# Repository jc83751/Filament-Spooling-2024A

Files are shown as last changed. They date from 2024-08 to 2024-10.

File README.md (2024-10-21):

# Filament-Spooling-2024A
DMMS Autumn 2024 - Filament Spooling Project.
Hello,
the material you see here was created in a 12 week period for a university subject. We hope that the compilation of materials produced
will be of good use to you.

You are free to use this in any way you like, however, should you publish anything from here please credit 
us for any work or research we have conducted as this took a lot of time and effort.

REF: Chu, J., Luu, M., Harris, J. & Do, D. (2024, August). _Filament Spooling 2024A_. GitHub repository. https://github.com/jc83751/Filament-Spooling-2024A

-J.C.

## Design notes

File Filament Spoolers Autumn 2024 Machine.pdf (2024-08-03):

# P20 – Filament Spoolers Design Documentation for DMMS Autumn 2024

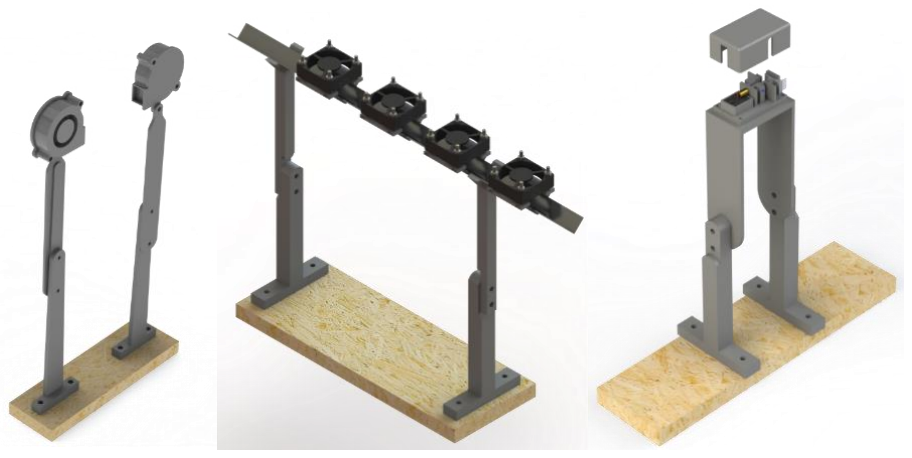
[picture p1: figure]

Project/ID
Plastic Filament Extruder for 3D Printing (P20) Clients

Richard Jamie
Marc Carmichael
Team

Jeremy Chu (14178077)

Johnathan Harris (13246160)

Duc Do (14317655)
Mark Luu (13199118)
Affiliation

UTS / ProtoSpace

43019 DMMS – P20 – Autumn 2024 – Filament Spoolers

2 | P a g e

## Table of Contents

## 1. Project Summary

### 1.1. Problem Statement

UTS staff, in specific, UTS ProtoSpace and FEIT, require the design of a filament spooler compatible with existing extruding technology that can produce 3D printing filament with consistent diameter (1.75 mm ±0.3 mm) and quality using recycled 3D prints and experimental materials. A system will be designed, allowing for the implementation of the filament spooler into existing operation, clarifying the feasibility and capabilities of the recycled or experimental 3D printing extruded filament in physicality.

### 1.2. Project Objectives

Key objectives are presented here as determined based on the functional requirements list and the evaluation criteria.

- Consistent Quality Filament Produced – The filament produced is of a diameter 1.75 mm with a tolerance of ±0.3 mm; the filament produced has consistent material properties throughout and deformation is minimised.
- Customisable Settings – The filament spooler has adjustable settings to accommodate a wide range of materials.
- Modular Design – The filament spooler is easy to assemble, upgrade, and has scalability for more general applications.
- Ease of Maintenance and Resources – The system of the filament spooler is easy to inspect, allowing for simple troubleshooting and official parts can be sourced domestically for change/replacement.
- Acceptable Efficiency – The filament spooler can produce a suitable amount of filament with minimal wastage.

### 1.3. Project Deliverables

Key Goals

- Filament Spooler – A functional model of the filament spooler capable of producing consistent-quality 3D printing filament using recycled 3D prints and experimental materials.
- Design and Next Steps Documentation – Basic instructions of operation, detailed technical drawings, schematics, and specifications of the filament spooler design, including assembly instructions and Bill of Materials (BOM).
- Filament Quality Assessment – Documentation of filament quality assessment procedures and results, mainly the measurements of diameter but may include material other properties.

Stretch Goals

- Machine Performance Evaluation – A report that evaluates the performance of the filament spooler involving efficiency, general reliability, and sustainability (e.g., plastic saved from landfill and electricity usage).
- Integration Plan – A proposed plan for the integration of the filament spooler at UTS, this could potentially involve collaboration with faculties such as Design, Architecture, and Building (DAB), FEIT Students, UTS Startups.
- Operation Manual – A user-friendly manual providing instructions for operating, maintaining, and troubleshooting the filament spooler.

## 2. Project Budget and Tasks

### 2.1. Project Budget and Plan

For this project, the P20 Team worked with a $600 AUD budget with flexibility regarding increases should it be required. This was presented in a client contract document where some key milestones were also proposed (see Table 1.) and agreed upon prior to starting work. It should be noted however that these were general milestones with the final delivery of the product occurring much later and in segments (agreed upon by the clients).

Table 1. Original Key Milestones Agreed Upon on 28/03/24
Task – Description | Expected Working Time | Approx. Start Time | Approx. Finishing Date
Project Scoping – Stakeholders interviewed to develop requirements and scope. Research conducted to guide activities and defined scope boundaries. Functional requirements and evaluation criteria will be created to validate the deliverables. | ~4 weeks | Start Week 2 | End Week 4
Translate and ideate – Stakeholder statements and needs are further refined to develop design concepts. Multiple designs will be presented and reviewed for the suitability of the project. | ~3 weeks | Start Week 4 | End Week 4
Refined Ideation – Design concepts, specifications, and ideas converge to a solution based on stakeholder(s) feedback and assessment. Rudimentary CAD and sketches will be developed to form a baseline for the chosen solution. | ~1 week | Start Week 4 | End Week 5
Prototype and Testing – Building a rudimentary model and testing its viability will be conducted to enable for refinement according to the evaluation criteria and functional requirements. | ~6 weeks | Start Week 6 | End Week 9
Deliverables (Documentation) – Design documentation, quality assessments, integration plans, performance evaluation, and an operation manual will be made. | ~7 weeks | Start Week 6 | End Week 12
Final Product (Gold Copy) – A product in an acceptable working state for the client is delivered. | ~11 weeks | Start Week 2 | End Week 12

Note that the week start, and ends are according to the UTS timetable as of 2024 – Autumn.

### 2.2. Project Tasks and Activities

There are many tasks and activities which were shared amongst P20 group members, these are nested amongst the design process (see Figure 1.). As such, only specific descriptions of tasks and activities will be briefly discussed.

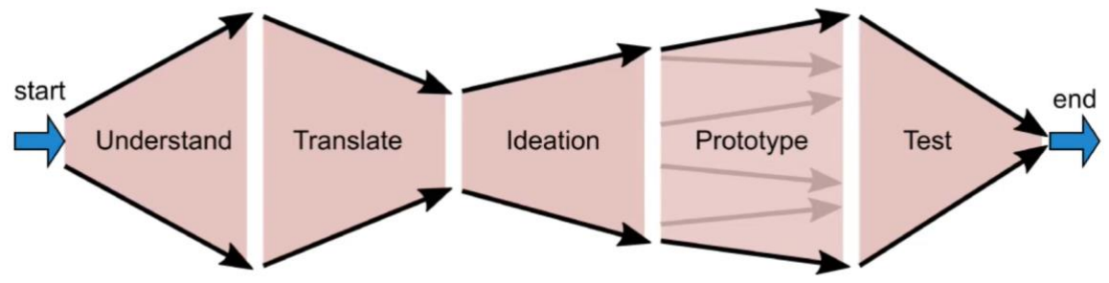
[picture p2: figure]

Figure 1. Overview of the Design Process (Carmichael, 2017). The main project tasks and activities undertaken in this project were:

- Scheduling tasks – Tasks to be scheduled amongst team members to prevent overlap, set-up accountability, and increase efficiency.
- Analysis and measurement of starting parameters
- Measurement of the Desktop SJ35 parameters (general dimensions, extrusion parameters, etc.).
- Analysis of previous groups work (in this case there was none).
- Properties of plastic pellets.
- Review of existing technology (literature review).
- Ordering of materials – Important to be done ASAP as delays are common (in this case there was a 4–5-week delay).
- CAD modelling
- Rapid prototyping of components in computer space.
- Construction of models for assembly.
- Sketching of drawings for documentation.
- Building and testing
- Translation of computer sketches to tangible components in a physical system.
- Testing of performance of the constructed system using experiments.
- Further iteration of constructed system.
- Documentation – Documentation of processes experienced, achievements, how to replicate experiments/results is crucial for the further development of an idea.

## 3. Responsibilities and Expectations

### 3.1. Cooling Subsystem

3.1.1. Responsibilities:
The cooling subsystem is an essential role of the extrusion process that manages the immediate heat dissipation of the filament and thereby, shrinking to a desired diameter. The responsibilities include having uniform rapid cooling, modular design such that the layout is interchangeable to accommodate and maintain compatibility of the other subsystems, and a design architecture that can self-adjust accordingly to variable conditions throughout the duration of the extrusion operation. Implementing controlled cooling minimises the effect of filament deformation and sustains the ideal material properties of the filament suitable for 3D printing.
3.1.2. Expectations:
The subsystem is expected to be simplistic, but modular like a closed feedback loop where real-time information such as the temperature and diameter size of the filament is known and self-calibrates to ensure the filament maintains within the 1.75 +/- 0.3 mm range. Cooling of filament to form a durable surface is crucial for it to be processed further in measuring and tensioning stages.

### 3.2. Measuring Subsystem

3.2.1. Responsibilities:
The measuring subsystem is a control design that allows the extruded filament to maintain the expected diameter. The laser system is controlled by an Arduino. The major function is to determine the drop in lux through the filament and thereby, use this conversion to determine the instantaneous diameter upon contact. The system is expected to be autonomous and does not require further input after starting operation.
3.2.2. Expectations:
The systems are expected to measure and convert the lux to the millimetres which is the diameters of the filament. This data is then used to ensure the filament is at the required 1.75mm diameter. If the filament is too small, the system will send a signal to the tensioning system to slow down so that the filament diameter increases. Similarly, If the filament is too big, the system will send a signal to the tensioning systems to increase the speed of pulling to decrease the diameters of filament.

### 3.3. Tensioning Subsystem

3.3.1. Responsibilities:
The tensioning system is the element which enables the precise control of filament diameter by effect of shear thinning. The assembly consists of Arduino-controlled rollers which grip and “pull” on freshly extruded and cooled filament at specific speeds to achieve diameter consistency. The relationship explained in brief is as follows:
- Faster roller speed = Thinner filament diameter, risk of snapping or stretching the filament too thin.
- Slower roller speed = Larger filament diameter, risk of clogging machine should the filament bunch up.
As such, it is critical that the extrusion rate of the extruder, the tensioning speed is finely tuned with the specific properties of a material to acquire a “goldilocks” zone of filament diameter (1.75 mm ±0.3 mm). Ideally, the speed of this system is informed by the results from the measuring subassembly.
3.3.2. Expectations:
The system is expected to be easily controlled using Arduino code using a specified speed according to the material extruded and the extrusion machine parameters. The system is also expected to not deform by squishing filament through its rollers, like soft pliable material such as TPU should be used to prevent unintentional deformation. Alternatively, an alternative spring type may be used according to material desired to be extruded and spooled.

### 3.4. Spooling Subsystem

3.4.1. Responsibilities:
Level Winding
The Level winding system is a location–based system that allows the extruded filament to be evenly distributed on an empty spool. This system is designed in sync to the Spooling. The Filament adjustor as shown in figure 2 helps maintain even winding by ensuring that each rotation will allow the filament adjustor the move in the x-direction incrementally to ensure the spool is neatly winded on during the process.

Figure 2. Filament Adjustor Spooling
The Spooling system is a speed-based system that's function is to wind the filament tightly around the spooler. The speed of this system is controlled in reference to the speed of the tensioning system. The system is a constant speed and is faster than the speed of the tensioner to ensure no build up filament between the two systems.

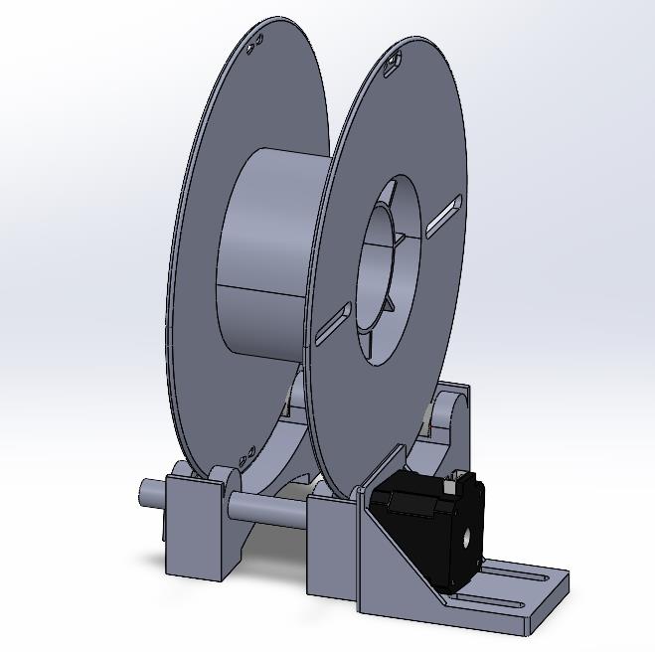
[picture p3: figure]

Figure 3. Spooling Sub-Assembly

3.4.2. Expectations:
Due to synchronisation problems. The leveller was not calibrated to provide even spooling for the entire duration of the systems operation. This occurred due to integration problems of the spool's rotational mathematics with the code of the spool. We also used two different Arduinos to control the tensioning – spooling system even though these two systems are intrinsically linked. This meant that one Arduino would have been perfect to control the system. The problem was that there were only two power pins in the Atmega 2560 for powering the motors (3.3V & 5 V). If we had more time to work on the system, we would have made an external power system using a breadboard to allow the joint system to be controlled from the one Arduino.
The filament extruder is an independent system that can ultimately change the systems performance. To ensure the system was producing desirable results, we set the filament extrusion rate at a constant that was considered optimal for the PLA material. These results were extrusion rate 400 (derived 5.5 RPM). Designing the tensioning –spooling system code to this setting was the only way to ensure quality filament and winding of the filament.

### 3.5. Overall System

Our filament extruder system for consists of four main subsystems (see Figure 4.). These systems are the cooling section, measurement section, tensioning section and the spooling section. Each group member has been assigned a subsystem as their main responsibility to design and prototype for proof of concept and be suitable for the overall assembly and operation of the extrusion process.
The Cooling system uses the air-cooling approach to lower the temperature of the filament at a constant rate to ensure the filament is rigid before reaching the tensioning system. This system works independently from the other system and has its own controller/autonomous functionality to change the speed of cooling.
The measurement system employs a laser and a light intensity sensor to detect light passing through the filament, with control implemented via an Arduino board and the Arduino IDE app. The system relies on rigorous testing to validate conversion of lux reading to diameter and relay real-time information to the other systems to adjust.
The tensioning system uses a belt and pulley-based design to drive rollers. The rollers drive the filament through to the next sub-system that is the spooling system. Pressure is placed on the filament to create friction to pull the filament. The system works based on the extrusion rate of the filament extruder and the measurements taken from the measuring system to calibrate the speed of the pulling action.
The spooling system uses a screw-based guide to evenly wind the filament on the spool. The system is linked to the tension system to match the speed of the spooler, however, may go faster should the spooling system spool faster than what is being extruded/tensioned, the spooling system will slip such that the filament does not break.

Figure 4. Components of the system to be designed. Red indicates features out of our main control, green highlights features required to be researched and developed by P20.

## 4. Communication and Key Stakeholders

### 4.1. Progress Report

The key stakeholders involve in this project were Mark Carmichael, Richard Jamie. Richard Jamie oversaw the filament extrusion project on site, and we went to him for advice and assistance in developing the project wherever he saw fit.
Richard suggested the idea of magnetic mounts to help remove the fans when feeding the filament through the system, this helped the safety issue of burning the user by contact with the extruder.
We had fortnightly meetings with Mark to provide updates on the progress of the assessment. During these meetings he would provide support on how to mitigate any problems that the project was presenting. He was able to help fix the spooling system by suggesting a spooling system that would slip when there was filament tension between the tensioning system and the spooling system. He also recommended a closed-feedback loop by using sensors to communicate if the filament is not the right diameter and automatically make the necessary adjustments.

### 4.2. Scheduling and Form of Contact

Every time we wanted to use the Protospacer Lab, Jeremy would email Richard for approval of using the lab for intended day and period.

### 4.3. Accessibility

Here is a brief list of important areas that we needed access to:

- Access to UTS Protospace
- Access to UTS Protolab
- Access to UTS Protospace 3D Printing
- FEIT Induction Access
- Access to Mechatronics Lab (Optional)

## 5. Status and Progress

### 5.1. Cooling Subsystem

5.1.1. Status:
The previous handover did not have an active cooling subsystem. It did, however, have components available for air cooling. Therefore, for this semester, rapid physical prototyping and testing was crucial to identify all internal and external issues concerning cooling the filament. The existing subsystem composes of the following:
- 3D-printed mounts for the system for height adjustment with the extruder nozzle
- Two DC 12V blower fans positioned at the extruding end for rapid cooling
- Aluminium V-shaped trough to guide the filament and provide additional heat dissipation
- Four BLDC 12V axial fans to cool uniformly along the trough
- All fans are controlled by manual PWM controllers for speed control
Now, simple modularity by having manual PWM controller toggles for both axial and blower fans are used to regulate voltage hence controlling the speed output of the fans. 3D printed mounting parts was necessary for ease of rapid prototyping and redesign should future groups intend to find more optimal design choices that meet the original project deliverables. The existing fans chosen were based on a balance between RPM speed, CFM (cooling coverage) and operational life that would justify cost-effectiveness as well as overall performance over extended periods of operation. Initially, a crescent-shaped trough was chosen to satisfy any size of filament produced and prevent the filament from reshaping on its own. However, the V-shaped was used instead for two reasons, proper design for 3D printed height support and for the fans ease of mounting.

Table 2. Cooling System Developments

Previous iteration: Crescent aluminium trough choice for unhindered movement of the filament to the next system.

Current Iteration: V-shaped aluminium trough for easier integration of 3D printed mounts and supports in rapid prototyping

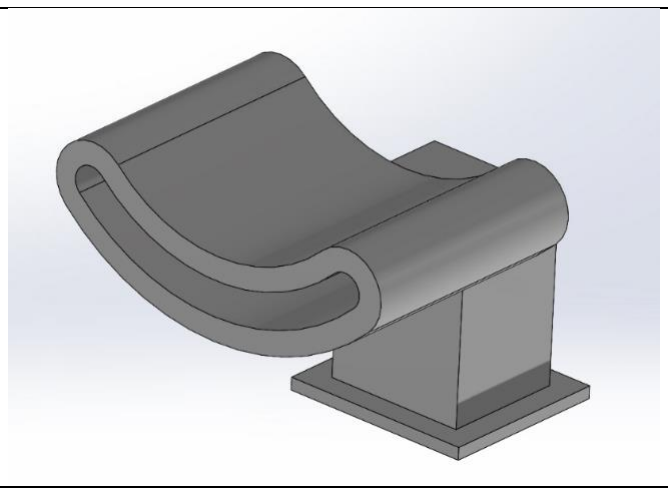
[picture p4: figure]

Previous trough support iteration: Awkward shape and tolerance with crescent trough (Also had slight warping despite listed product dimensions)

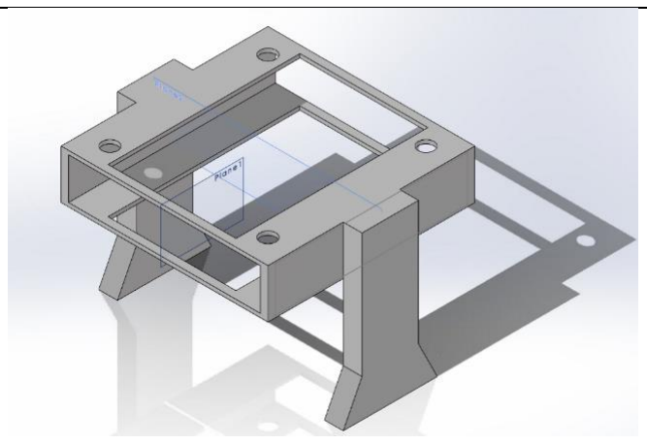
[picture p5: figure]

Previous fan mount iteration: Screw mounts and support of fans needed to be designed on top of the trough, also was not fully 3D print compatible.

Current system (Axial): Axial Fans all connected to a breadboard and controlled by a single manual PWM controller for speed control

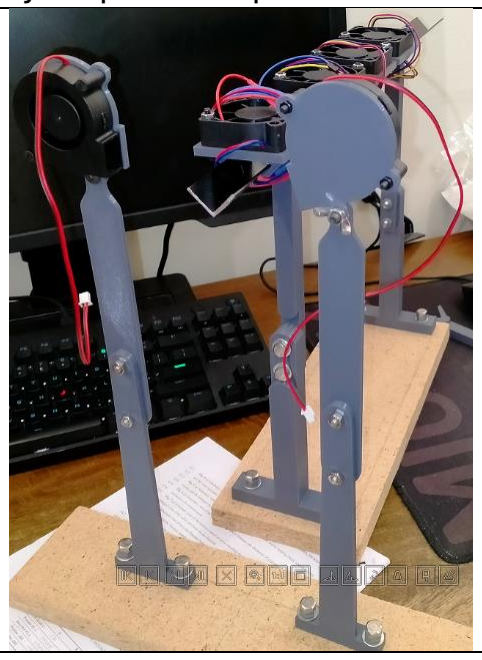
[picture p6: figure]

Current system (Blower):
Blower/Centrifugal Fans connected to a breadboard (same one as axial) using a separate manual PWM controller for instantaneous cooling at the filament upon immediate extrusion. Each fan has its own support with adjusters to angle the fans as required for optimal cooling.

Current cooling layout: Mounted fans on a V-shaped aluminium trough held by screwed-in V-shaped supports.

5.1.2. Progress:

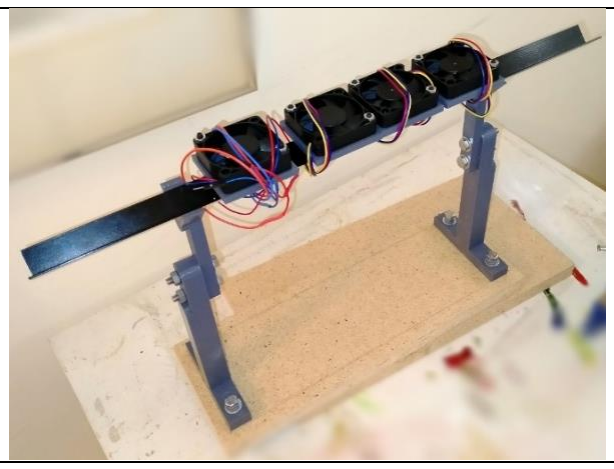
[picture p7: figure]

Further testing with the existing subsystem is essential to determine if further improvements should be implemented. Referring to the “Machine Testing Experiments and Results” document, three experiments have been conducted to rigorously test the consistency and performance up to 6 hours of continuous operation. The cooling system is effective functionally. However, it still requires more data for verification on cooling efficiency and knowing exactly which areas of improvements can dramatically increase results.

### 5.2. Measuring Subsystem

5.2.1. Status:
When reviewing the handover documents of the previous group, they did not have a clear measuring system as they were using the principle of measuring the displacement of the magnet and measuring the strength of it. (Figure 5).

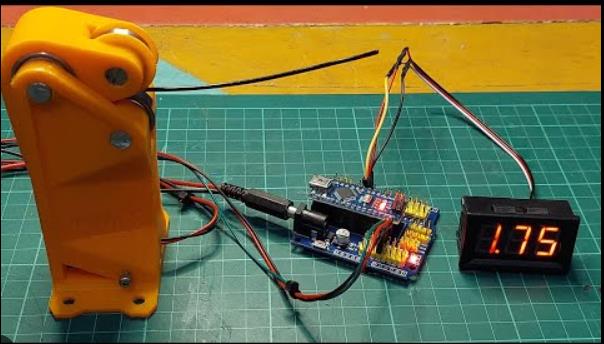
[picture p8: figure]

Figure 5. Measuring filament diameter base on the strength of the magnet and displacement (Hendra P Syahputra, 2022)

There was little explanation written about how it works or if there was any existing model left behind, so it was assumed that the product failed to produce accurate reading. Therefore, rapid researching and testing was urgent to determine the best device to measure the filament diameters. Based on the research from the file “Analyse Filament Measure”, we can see there are four main concepts that can be tested which are the ultrasonic sensor, light sensor, digital caliper and the time-of-flight sensor.

Figure 6. (a) Ultrasonic sensor; (b) Light sensor; (c) Digital calliper; (d) Time-of-flight sensor
Based on the four potential options, we decided to go with the light sensor and the digital caliper. The reason is based on the literature review from lee et al., 2018, the extruder projects that have produced promising results and for the caliper, it was based on a YouTube tutorial from Electronoobs, 2019 which showed practical implementation of the redesigned caliper producing accurate readings.

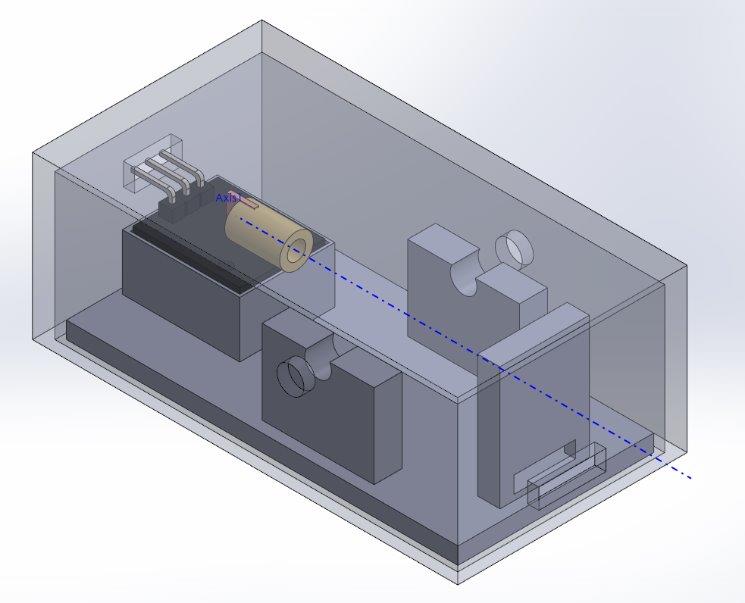
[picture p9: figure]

Figure 7. Laser and Light sensor model Based on the information above, the current system design is a combination of the laser sensor and the calliper to measure the filament diameters but due to incorrect equipment purchase and error of bit count of the calliper, this was not fully realised. For the laser sensor, the first design was getting mixed and nonsensical data which we discussed is due to the filament not being stable on the holder for the laser to detect plus the sensor picking up reflected light from inside of the chamber. (note: I have also tested the ultrasonic sensor, but it can only go down to 1cm which is not enough resolution for the job).
5.2.2. Progress:
Due the continuous error of the bit count and the pin output being incorrect (figure 8), the best decision moving forward was to remove the calliper from the design and follow through with using only the laser sensor. Although there were still issues for example, with the data being mixed with the create model in figure 7 due to the filament not being stable for the sensor to detect it correctly, troubleshooting was easier to handle.

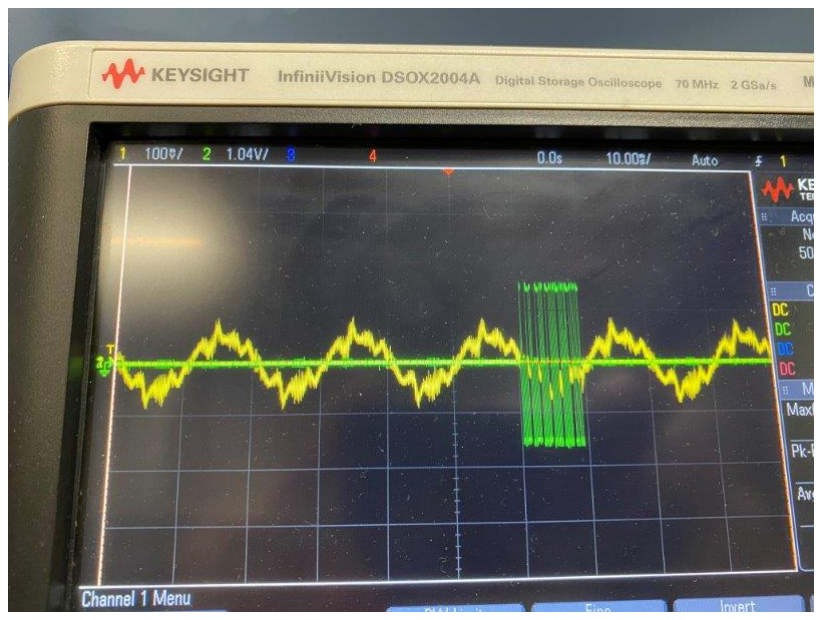
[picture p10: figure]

Figure 8. Fail Result from Calliper from incorrect bit count.

For the new design for the laser (figure 33 in the appendix), a silicon base hole was included to allow the filament to run through without any issues. Additional redesigns were creating a smaller hole size reduced the error of filament vertical free motion as it passed through and having the position of the filament closer to the laser for better direct contact on the filament, marginally improving data readings. The other change to the design was adding a filter for the laser when reaching the sensor (a piece of paper). This is to ensure the data receiving is correct.

### 5.3. Tensioning Subsystem

5.3.1. Status:
The previous group did not have any tensioning mechanism or parts needed for one; this was concerning as by review of literature finds that a tensioning subassembly is a critical component which maintains a desired filament diameter. As such, the rapid prototyping of this subsystem was performed as early as Week 4. These can be briefly viewed in Figures 9 – 10. The final tensioner device constructed is illustrated in Figure 11. To see the design files, please refer to the Appendix.

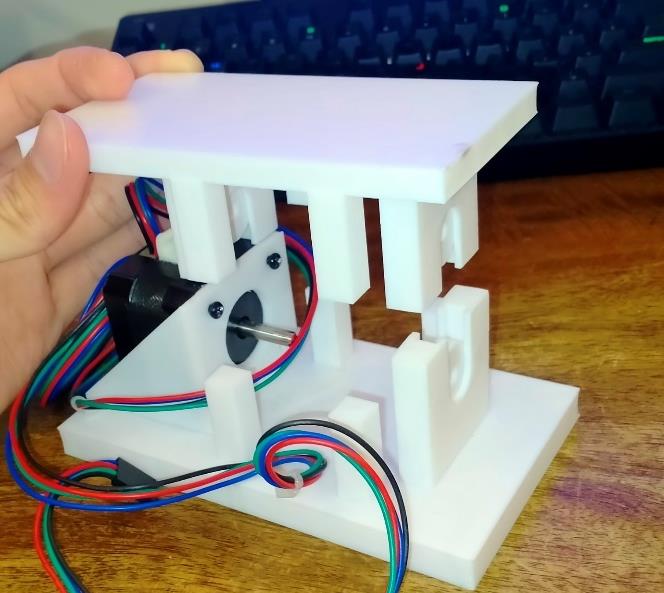
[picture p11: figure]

Figure 9. Shows the first iteration of the tensioning device, left being the CAD model, right being the partially realised model. The 4x tension spring design was determined unfeasible due to complex geometry, poor manufacturability, and reliability concerns.

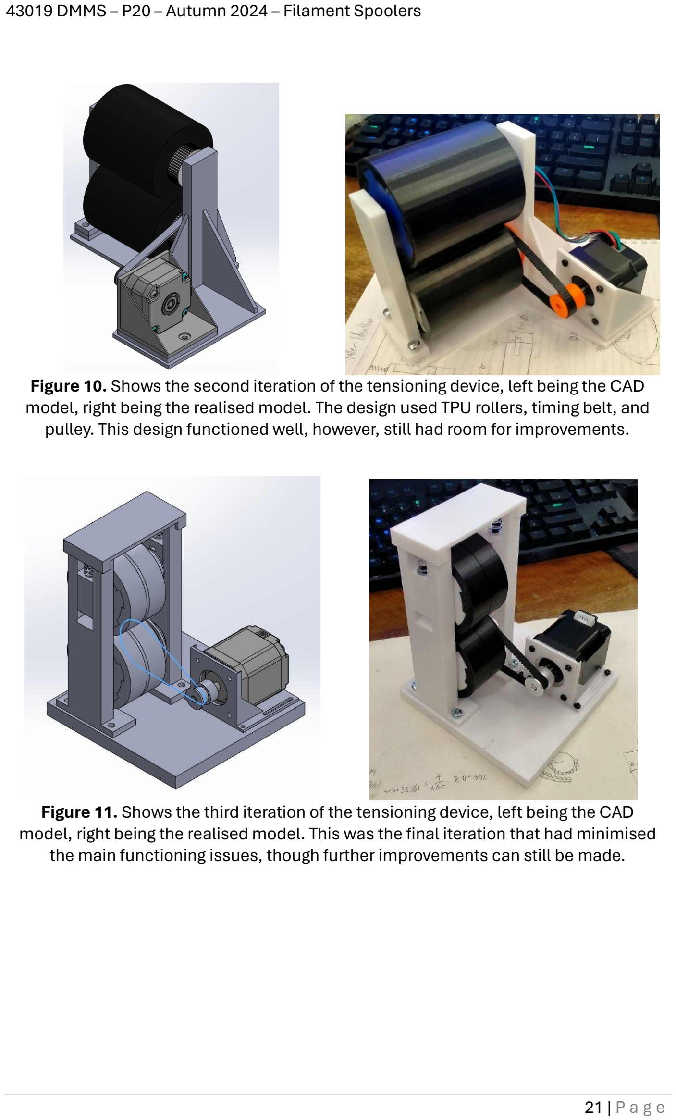
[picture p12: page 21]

Figure 10. Shows the second iteration of the tensioning device, left being the CAD model, right being the realised model. The design used TPU rollers, timing belt, and pulley. This design functioned well, however, still had room for improvements.

Figure 11. Shows the third iteration of the tensioning device, left being the CAD model, right being the realised model. This was the final iteration that had minimised the main functioning issues, though further improvements can still be made.

5.3.2. Progress:
The third iteration of the design performs well and with a high degree of control. Please refer to the “Machine Testing Experiments and Results” document for further details. To summarise current progress, an excel document (see Appendix) was made which correlates extrusion machines (Desktop SJ35) gauge reading to its auger RPM (see Figure 12.). A speed of 410, correlating to approximately 5.5 RPM was chosen for most

Figure 12. Shows the gauge reading of the Desktop SJ35 extruder’s auger to its actual RPM.
The material experimented within this session was labelled as 1588ATL, though, beyond this no further information could be found. To test the ability of the tensioner to alter filament diameter, different speeding settings (refer to the Excel document in the appendix) was performed, results of which can be viewed in Figure 13.
| | Rough Interp: RPM = 0.0133*Gauge Reading + 0.0396

100 200 300 400 500 600 700 800 900 1000 1100 1200 1300 1400

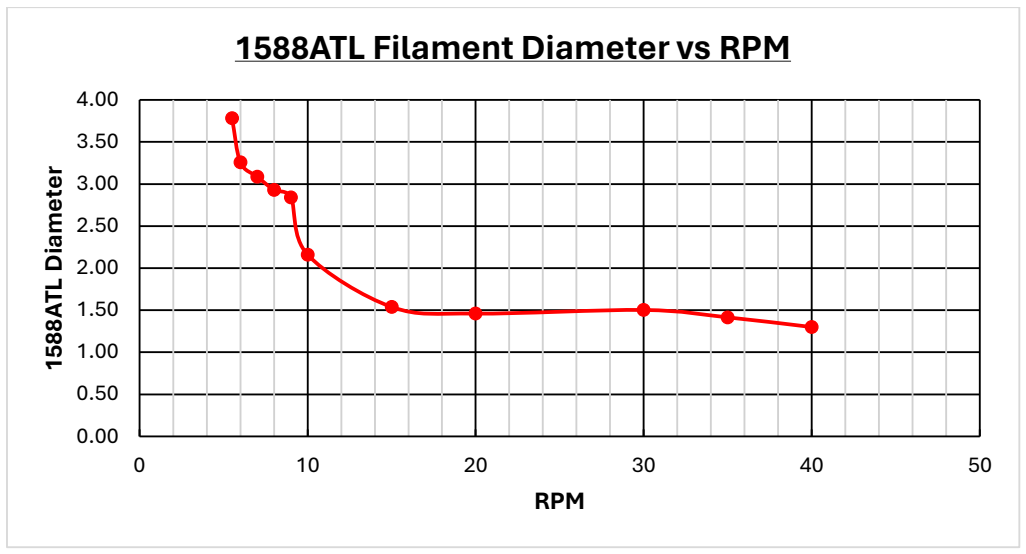
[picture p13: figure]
1588ATL Diameter; RPM; 1588ATL Filament Diameter vs RPM

Figure 13. Shows experimental results correlating RPM of tensioner roller speed to 1588ATL diameter.

### 5.4. Spooling Subsystem

5.4.1. Status:
Level Winding
The level winding system was not considered to be updated until the very end of the project. Marc presented the idea of an x-end stopper for calibration purposes. The need for improving this system did not present itself due sense of urgency to get the level winder to accurately adjust for the whole duration of the test.
5.4.2. Progress:
Spooling
The original system comprised of a spooler fixed on an aluminium shaft. This shaft controlled the rotation of the empty filament spool. It was determined that if the speed is not matching the tensioning speed due to human input, it can create the risk of ripping the filament apart from the system. This discussed the possibility of adding a sensor to communicate the speed of the filament, however, was disregarded due to over-engineering and still due to present risk of breaking the filament if the speeds are not exactly matched. Therefore, a new design was proposed that allows the spooler to rotate at a fixed speed without the need to accommodate to the increase in spool circumference or if the tensioning system changes speed. The idea was to control the speed of the spool by putting in on top of the rotating pulleys. If the speed of the filament is too slow in comparison to the spooling rotation, then tension will occur causing the spooler to slip on top of the pulley and the given bearings. At the time, there was no other way around. If the rotation is too slow, too much filament will build up between the spooling system and the tensioning system leading to some fault caused by entanglement. We thus settled for an angular velocity that will always be faster than the tensioning system. This will cause slipping to occur, however no entanglement problems.

### 5.5. Overall System

Based on the status of the project, producing filament of consistent diameter was very viable. However, there were issues with two systems, the Measurement system and the Spooling system. These systems could not be completed due to time constraints and equipment failure. Improvement of each system could include:
Cooling system
There is sufficient cooling for the filament to the point that it maintained its shape within 0.2-0.5mm of its desired diameter when moving through the tensioner which is a great success. However, air cooling was not fully effective in cooling down the filament completely as at higher temperatures (>150) passing through the systems, heat can still be detected from within the filament which may reduce the quality of the filament. Therefore, recommendations are to either focus purely on improving the existing system or determine if water cooling could increase the cooling efficiency. At the time of the status, water cooling was not an option due to two reasons: One, ProtoSpace does not permit water technology in the ProtoLab and two, most options were very expensive, almost to the industry level.
Measurement system
Detecting the filament lux was found possible but failed to produce the correct filament diameter. This data incompatibility resulted from the detection which causes the conversion equation from lux to millimetres to be inaccurate and produce undesirable data. The measurement system can control the speed of the tensioning system; however, this feedback loop is not executed until one rotation of the tensioning system has completed. By the time one revolution is completed, a few centimetres of filament have already been extruded. Thus, proving the time is too long. As a result, it is recommended a calliper is used to measure the filament correctly and using threading in the coding block to complete multiple tasks at the same time.
Tensioning system
It was successful to draw and feed filament to the next system consistently, however, the system needed the filament to be manually placed through and occasionally, the filament would skip and miss the tensioner. So, it is recommended creating a guiding system to make the process more reliable.

Spooling System
Spooling the filament was successful and the system would slip whenever the filament tension was too great. This was executed well as the slipping could occur without breaking the filament. However, due to time constraints and 3D printing parts failure, fully testing the system to determine its effectiveness in winding and correctly guiding the filament through was not conducted. In addition, the spool sometimes would skip and stall until manual intervention. This may be due to the weight issue or the bearing connecting with the spool. Therefore, recommendations are changing the connection between the spool and the motor turning to increase friction.

## 6. Known Issues and Challenges

### 6.1. Initial Assumptions

For the assumption of this project, there were three aspects to consider:

- Environmental conditions
- Operation parameters
- Raw material quality
When looking at environmental conditions, the machine will only be used indoors with maintained standard temperatures (20-25 degrees) and humidity (30-50%). For the operational parameters, the machine will work a maximum of 8 hours a day since ProtoSpace does not permit the machine to work unattended or beyond hours. It is also assumed that the extrusion rate is constant. Lastly, for the raw material quality, it is assumed that the pellets used is correctly processed and free of contaminants. This is to ensure every product produced is uniform and the data collected is correct.

### 6.2. Risk Analysis

Based on the current setup of the project, a contingency plan is necessary to address potential issues. A table has been made to show what problems can occur, what level of risk they have and the countermeasures in place to ensure that issues can be dealt with.

Table 3. Risk Analysis
Problems | Rate Problem (1-25) | Likelihood (1-5) | Consequence (1-5) | Countermeasure
Equipment Failure | 6 | 3 | 2 | maintenance, high quality parts
Raw Material Contamination | 8 | 2 | 4 | Checking material before usage, buy material from reliable source
Health and safety hazards | 15 | 3 | 5 | Ensure all safety protocol are followed, wear PPE, ensure proper ventilation for certain materials

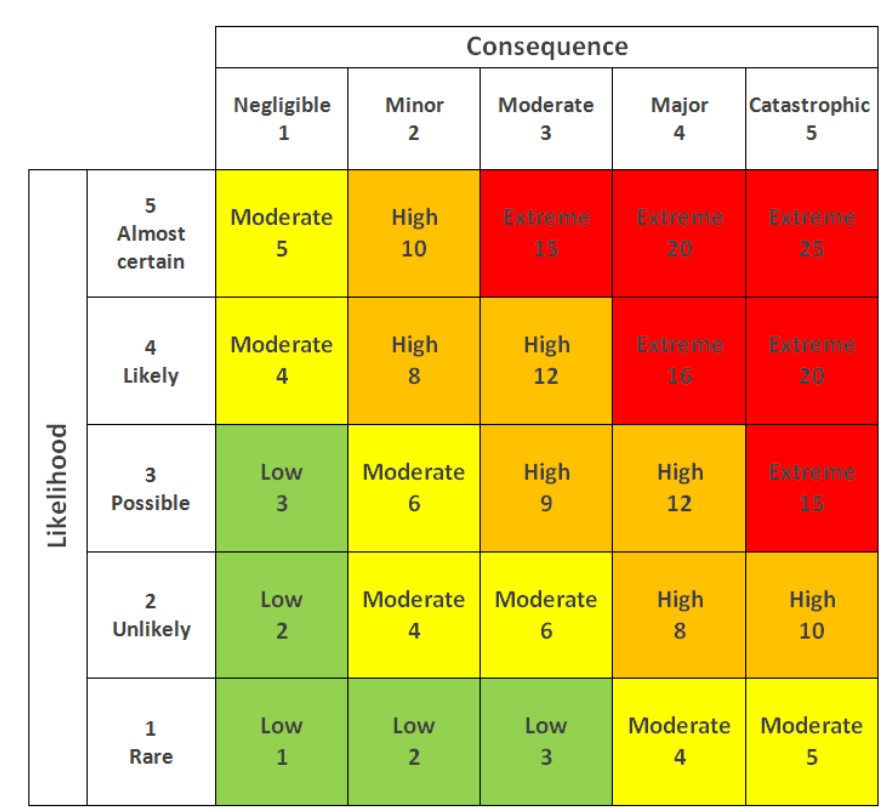
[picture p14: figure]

Figure 14. Risk Scale (Guthrie, 2020)

## 7. Recommendations

Parts orders occurred between Sprints 2 to 3; While personal parts were incorporated for substitution during testing, it is highly recommended to source and confirm purchases to prevent delay in project progress. Despite ordering “relatively” early on 02/05/24, our first parts only started arriving on 03/05/24 despite ordering from Australian distributers. External stakeholders encountered was the Design, Architecture and Building (DAB) Department where their shredder may be used for the shredding of 3D prints for recycling. A problem encountered with their machine is their mesh filtering component which would separate finer usable shredded particles from larger unusable ones. Currently, their mesh size is larger than what would be required for this project’s application. Please see the attached document “DAB – Tony Meeting – 08.03.24” for more information.

### 7.1. Cooling Subsystem

The next steps for the cooling subsystem are designing advanced closed-loop feedback architecture. This can be done in two suggested paths, however, innovative approach outside of these paths is also open to implementation if the overall methodology maintains efficiency and modularity that will sustain the filament material quality.
The first suggestion is having the cooling subsystem change based on temperature. This can be done through temperature sensors contacting directly with the filament to transmit real-time data for self-adjustment. The other suggestion is working alongside the other subsystem to adjust according to the tension levels of the filament and the output reading of the measuring subsystem for size correction. Both methods are intended to be autonomous and differ by being either independent or, co-dependent on the subsequent systems.
As forementioned in the “Machine Testing Experiments and Results” document, testing the system will validate how optimal the system is functioning. As a suggestion from previous sprints, determine the best forms of heat dissipation whether it is from material, improving the cooling of the extruder itself or re-design. Revision of knowledge such as heat transfer analysis is recommended to evidently provide accuracy and having known hypothetical results before evaluating the experimental analysis.

### 7.2. Measuring Subsystem

The system is well designed in its ability to measure the correct lux associated with the filament diameters; however, it contains multiple flaws.
7.2.1. Changing for different filament material
For the current system, it can only measure one material at a time. This is due to the conversion equation from lux to millimetre of the filament (not yet correct). Since each material has different properties which reflect different light level, additional instructions will be required should another material be spooled. The authors recommend using a different type of measuring device such as a time-of-flight sensor to measure the filament diameter or a four pin output data calliper to measure but make sure it can correctly produce the data output. Further research into measuring systems is encouraged.
7.2.2. Laser sensors data change if move filament through after a period
For the current setup in figure M, it is shown that the laser is consistently on which the light from the laser is shining onto the sensor. This has caused the measurement data of the laser to decrease overtime and reduce the accuracy of the measurement. This is due to many reasons such as thermal effects, saturation of light photo-bleaching and degradation of the sensor due to too much exposure or long-time exposure to the laser. Also, the laser has some issue with connection as the soldering part is not good and may require regular maintenance. Using a different type of laser or turning off the laser when not using is a suggestion. In addition, using other methods of measuring filament like calliper or time-of-flight sensor to measure the diameters is also a recommendation.
7.2.3. Coding cannot take consistence measurement
For the current Arduino coding for the measurement of lux, it can take the lux measurement consistently, however if it is connected to other systems, there will be a delay. This is due to the structure of the software of the loop. Since it must complete the whole code to repeat the process of measuring the filament again. This creates error and reduces the ability to control filament accuracy immediately. It is recommended to use the thread function to run multiple tasks at the same time such as the TaskScheduler library (see Figure 15.) or use a different controlling system other than the Arduino to manage the systems like Raspberry Pi.

Figure 15. Shows the TaskScheduler library in Arduino.

### 7.3. Tensioning Subsystem

Recommendations for the tensioning subsystem will be listed in dot points as follows:

- Spring constant – Acquire a spring with a known or determine the spring constant of the current spring to perform relevant calculations which may impact slippage and compressive forces acting on the filament tensioned.
- Adjustable Spring – The spring force causing the gripping action could have a mechanism which allows for its adjustability.
- Rollers – Experiment with varying roller diameters and materials. Additionally, experiment with different filament slots sizes and shapes (the indentation at the centre of the roller).
- Torque increasers – currently a timing belt is used to increase the torque of the tollers. An alternative method of achieving this may be the use of a geared-stepper motor.
- Belt and pulley placement – currently the belt installed, though possess some tension, still has slack which is problematic should one wish to increase speeds. This problem may be remediated if the stepper motor bracket positioning slots could be easily adjusted then tightened on its base.

### 7.4. Spooling Subsystem – Winding

7.4.1. Accommodate different sized spools.

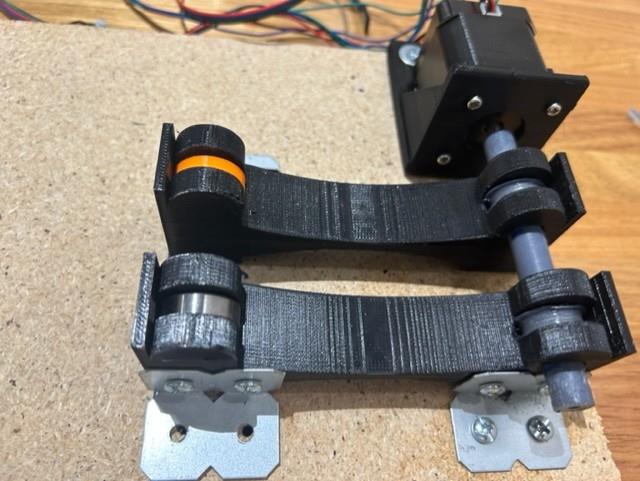
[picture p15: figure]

Figure 16. Winding control sub-system. The winding system is drawn by two pulleys connected to a shaft (Figure 16). To stop the pulleys from slipping the pulleys were superglued to the shaft to ensure translation of the motor to the pulleys. Thus meaning, each pulley was fixed at that position on the shaft and only once spooler was suitable to this system.

7.4.2. Better Winding gears/pulley system.
Building on from 6.4.1, the pulleys that were used to drive the system were slipping due to the contact area and a low coefficient of static friction between the two materials. To fix this issue we used double sided tape on the pulleys to help drive the spooling system. Overtime the tape would lose its stickiness and the spooling system would constantly slip. In the future a completely new winding system will be necessary with a new gearing system that will promise winding at both low and high speeds. This system will also need bearing that cause the spooler to slip in the case of tension.

### 7.5. Spooling Subsystem – Leveling

7.5.1. x-end stopper to home leveller.

Figure 17. End-Stopper limit switch. Just like in a 3D printer that adjusts its position every time it turns on, the same principle can be applied to the levelling system to ensure that the location of the level winder is proportional to the amount of filament that is coming out of it. This can also prevent the motor from stalling if it reaches to far the right or too far to the left.

### 7.6. Overall recommendations

- The system (excluding the extruder) should ideally run on one power supply (currently power needs to be supplied individually to: the cooling system, measuring (not functioning), tensioning, and spooling subsystems.
- The system should ideally run on one computer (currently 2-3 Arduino’s are required).
- The system should have a user-interface and allow the user to change the settings in accordance with the extruder
- Create an accurate CAD model of the Desktop SJ35 extruder in SolidWorks.
- The current extruding machine (Desktop SJ35) is tall which makes it inconvenient to align parts as a stand is needed. Create a long-term solution stand which is easily adaptable such that this height dilemma is not an issue.
- Should one wish to modify the entire system this will be surprisingly useful.

- As not all CAD files are available, are of differing versions, or have design faults with them, it is recommended that the next team reference our sketches and recreate the CAD models.
- Coding solutions should be found to integrate all four systems into one Arduino. Alternatively, use a different, more appropriate solution.
- Coding solutions for improving feedback loop for measuring-tensioning system. (The use of Threading). (Note Arduino does not support threading).
- Coding solution for level winding system + the integration of an x-stopper to home system.
- Improved spool-winding system to accommodate large spool sizes.
- Water cooling system instead of fans.
- Use standard fastener sizes for the designs.
- Redesign measuring subassembly since the current required a lot of calibration to work correctly.
- System should be fixed to a wooden base to improve portability of the system.
- Tensioning system should have guider to ensure the filament stays on the pulley
- Other filament types should be considered (Velostat, PVA, ABS etc).

## 8. References

Carmichael, M. (2017, March 18). V2.1 Overview of the Design Process [Video]. YouTube https://www.youtube.com/watch?v=SY0uivnmB0s
Electronoobs. (2019, June 9). 3D filament meter caliper Arduino i2c tutorial. https://electronoobs.com/eng_arduino_tut93.php
Guthrie, G. (2020, November 4). Qualitative risk analysis vs quantitative risk analysis: What’s the difference? Nulab. https://nulab.com/learn/project-management/qualitative-risk-analysis-vs-quantitative-risk-analysis-whats-difference/ (https://nulab.com/learn/project-management/qualitative-risk-analysis-vs-quantitative-risk-analysis-whats-difference/)
Random Nerd Tutorials. (2022, March 10). Arduino with BH1750 Ambient Light Sensor | Random Nerd Tutorials. Random Nerd Tutorials.
https://randomnerdtutorials.com/arduino-bh1750-ambient-light-sensor/ Hendra P Syahputra. (2022, April 16). Desktop Filament Extruder Pt 2 : Diameter Sensor #filamentextruder #3dprinting #3dprinter #arduino. YouTube. https://www.youtube.com/watch?v=vE6tmdFhxbk

## 9. Appendix

### 9.1. Microsoft Teams Planning - Jeremy

Figure 18. Filament Teams channel

Figure 19. Teams Channel – Research

### 9.2. Meeting Minutes

- See attached document, “Meeting Minutes”

### 9.3. Assembly Instructions

- See 3D CAD Files

### 9.4. Technical Drawings – Jeremy and Jonathan

- See attached Engineering Drawings

### 9.5. Wiring Schematics – Mark

NOTE: The wiring schematics shown are similar examples to the existing system. Due to time constraints, high-level detailed diagrams could not be made. However, the overall system is relatively intact thereby, should provide ease of understanding the wiring structure of each system in real observation.
9.5.1. Measurer Wire Schematic

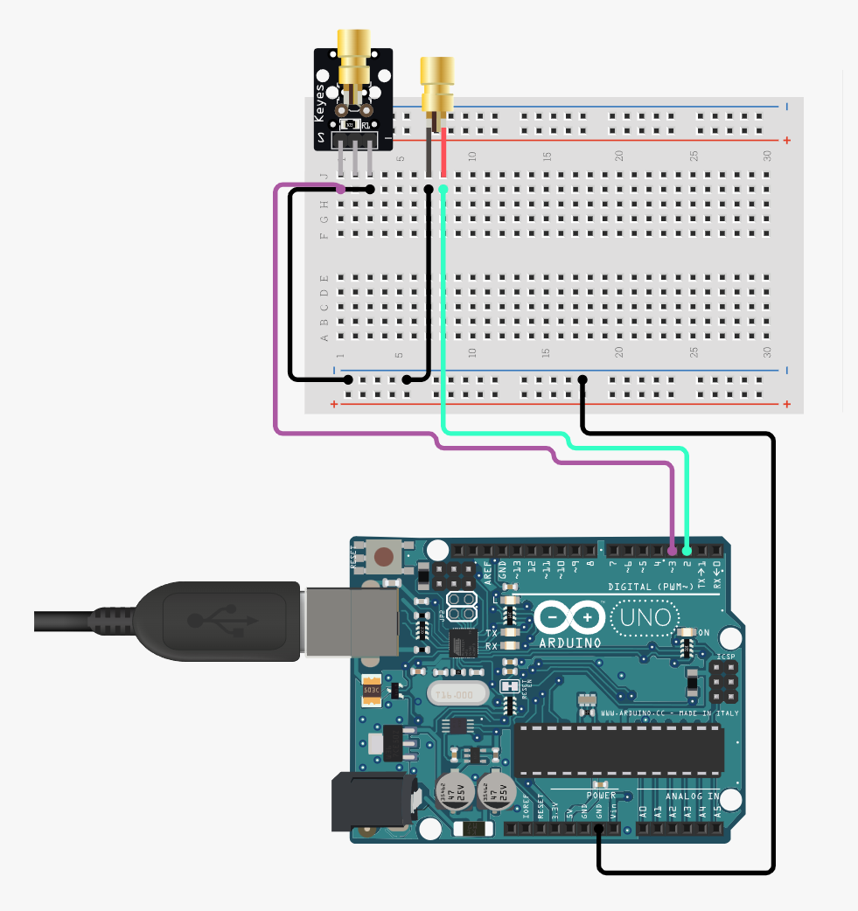
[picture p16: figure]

Figure 20 (a). Measure Wire Schematic

Figure 20 (b). Measure Wire Schematic

9.5.2. Light Sensor Wiring Schematic (Random Nerd Tutorials, 2022)

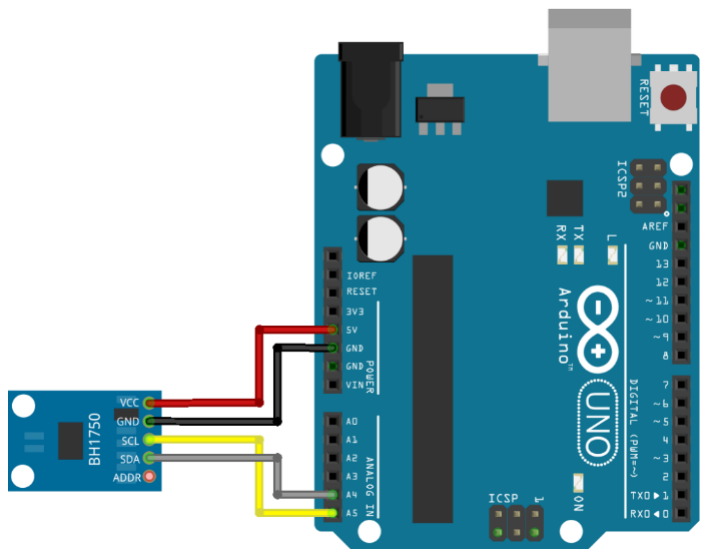
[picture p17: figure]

Figure 21. Light sensor wiring schematic. (Random Nerd tutorials, 2022).
9.5.3. Calliper Sensor Measuring Wire Schematic (Potential) (Electronoobs, 2019)

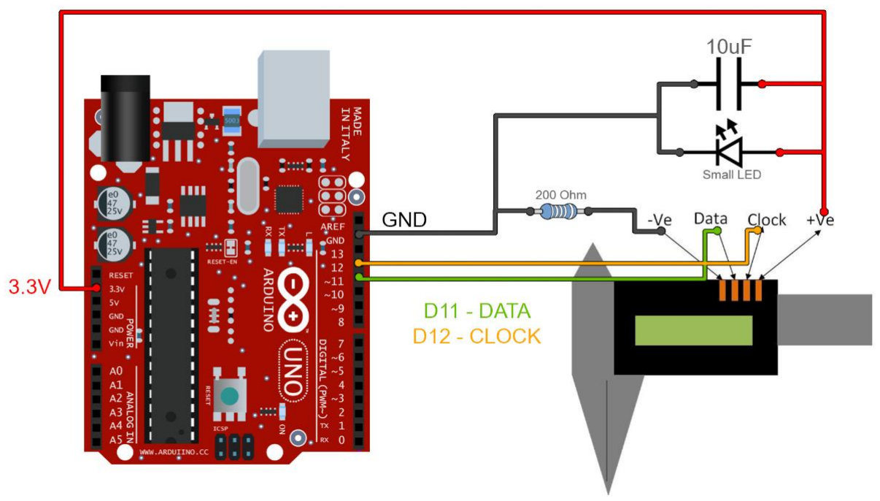
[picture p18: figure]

Figure 22. Caliper sensor Measuring wire schematic. (Electronoobs, 2019).

9.5.4. Cooling Wire Schematic

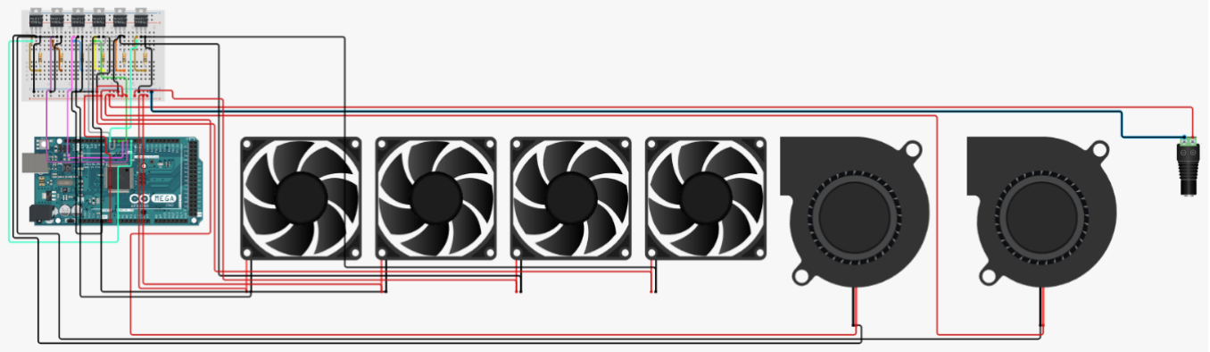
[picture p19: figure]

Figure 23. Cooling Wire Schematic

9.5.5. Stepper Motor Control for Winding/Tensioning Wire Schematic

Figure 24. Stepper Motor Control for Winding/Tensioning Wire Schematic

### 9.6. Coding

9.6.1. Cooling systems

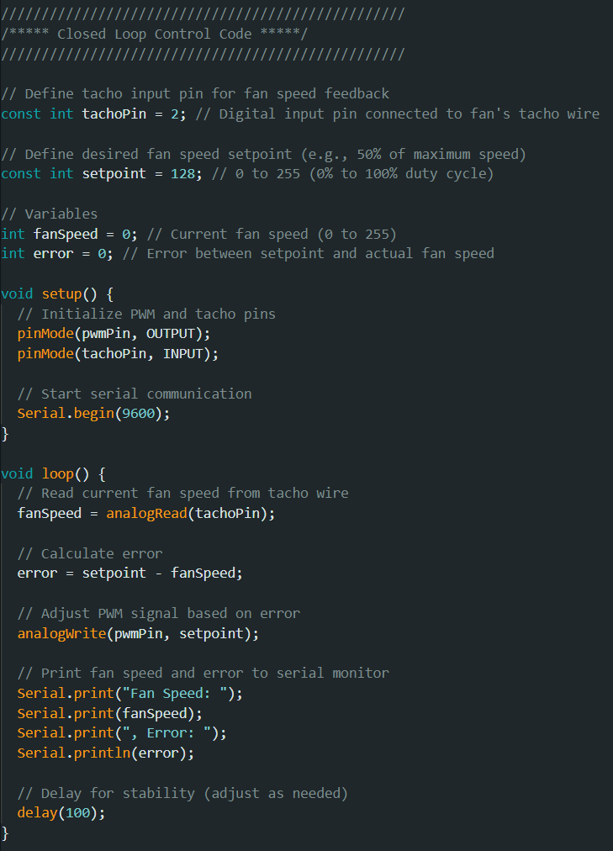
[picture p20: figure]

Figure 25. Closed-loop control code - Fan

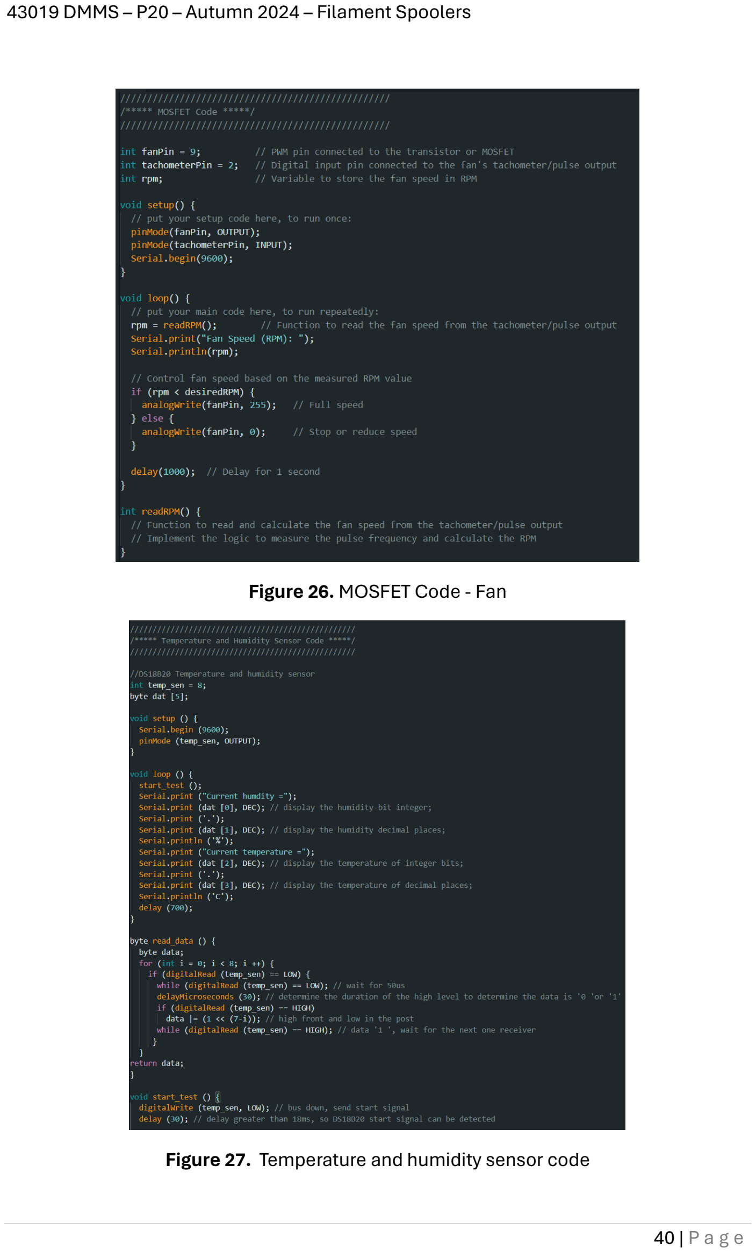
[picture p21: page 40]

Figure 26. MOSFET Code - Fan

Figure 27. Temperature and humidity sensor code

9.6.2. Tensioning systems
Note: With this code, if the step count exceeds that of 1 full revolution with any intermediate step afterwards (e.g., a delay(X) function), abnormalities occur. As such, if you wanted this stepper motor to rotate 2 revolutions only and pause for 1 second, you will need to repeat the myStepper.step(X) function 2 times.

Figure 28. Tensioning system Code.
9.6.3. Measuring systems
Note: Before running the code, some libraries are required to run the sensor

Figure 29. Library for Sensor Control

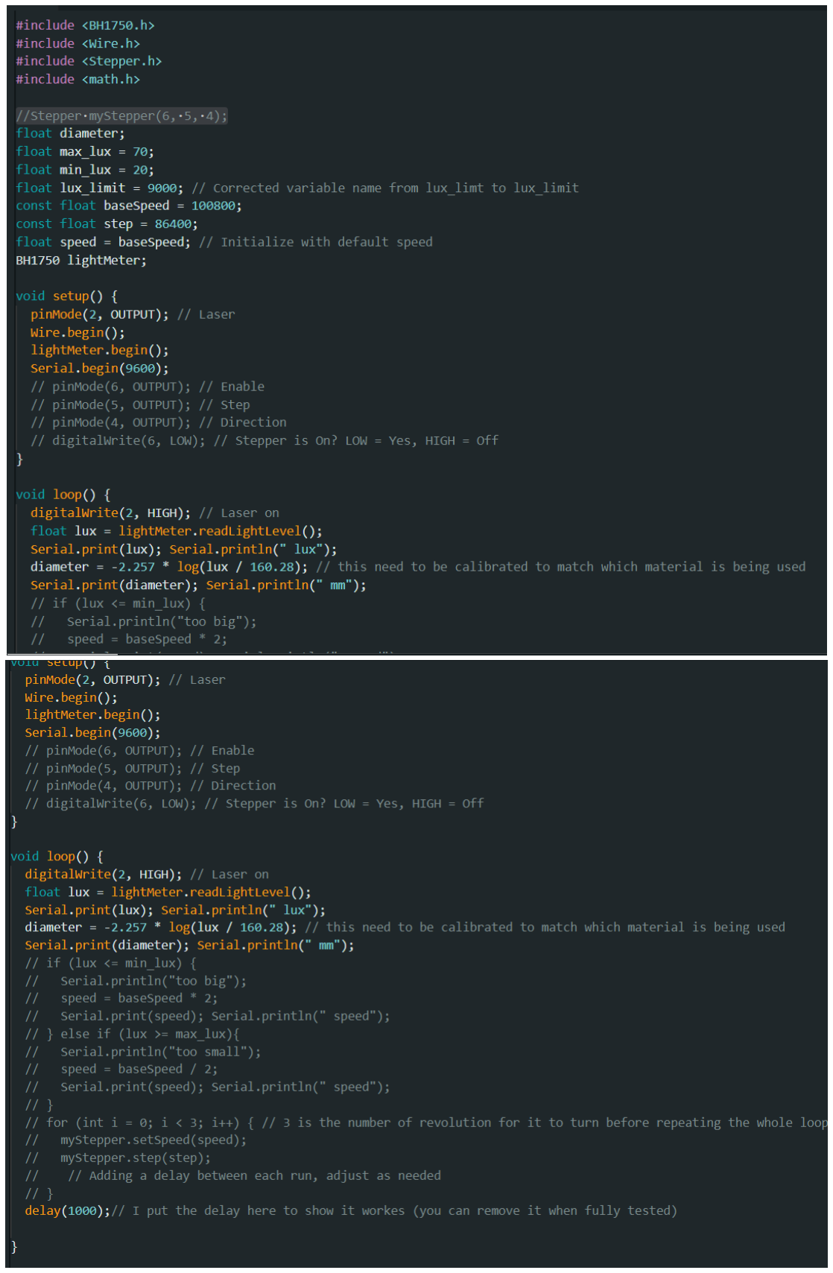
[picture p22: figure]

Figure 30. Code for Measuring system.

9.6.4. Level - Winding system

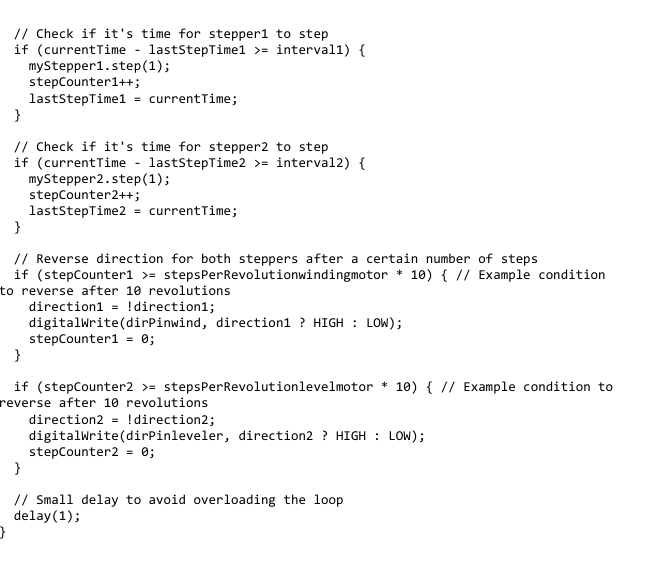
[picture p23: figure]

Figure 31. Level – Winding system code

### 9.7. Measuring System – Pictures of what was attempted

Figure 32.

Figure 33.

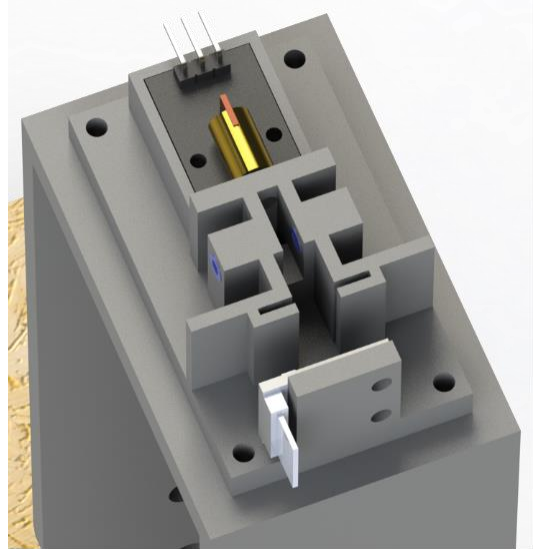
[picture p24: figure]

Figure 34.

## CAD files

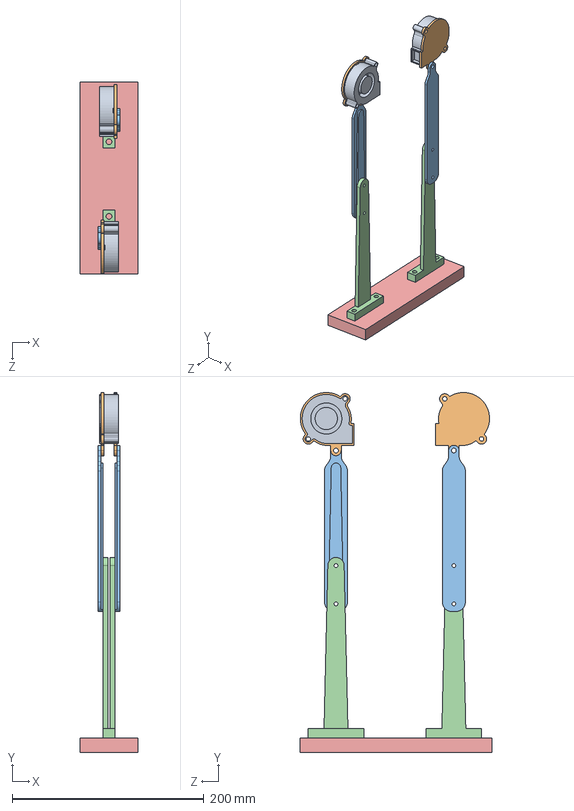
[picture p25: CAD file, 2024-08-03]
Cooling CAD/Centrifugal Cooling/CentrifugalCooling Assembly.SLDASM
60.0 x 375.5 x 200.0 mm
Centrifugal-fan x 2
CentrifugalFan-Bracket x 2
CentrifugalFan-HeightArm x 2
CentrifugalFan-Base x 2
CentrifugalCooling-WoodBase

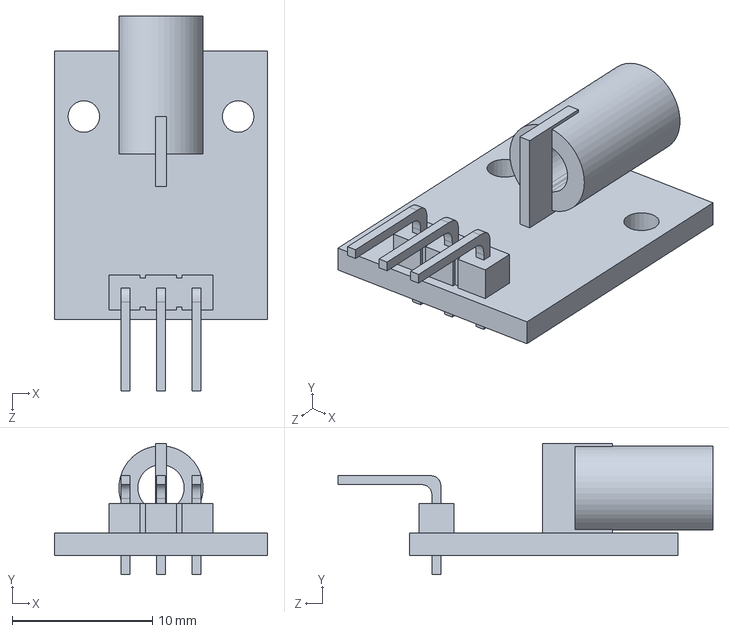
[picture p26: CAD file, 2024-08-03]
Measuring CAD/MeasuringModule-V3.SLDASM
15.2 x 9.36 x 26.7 mm

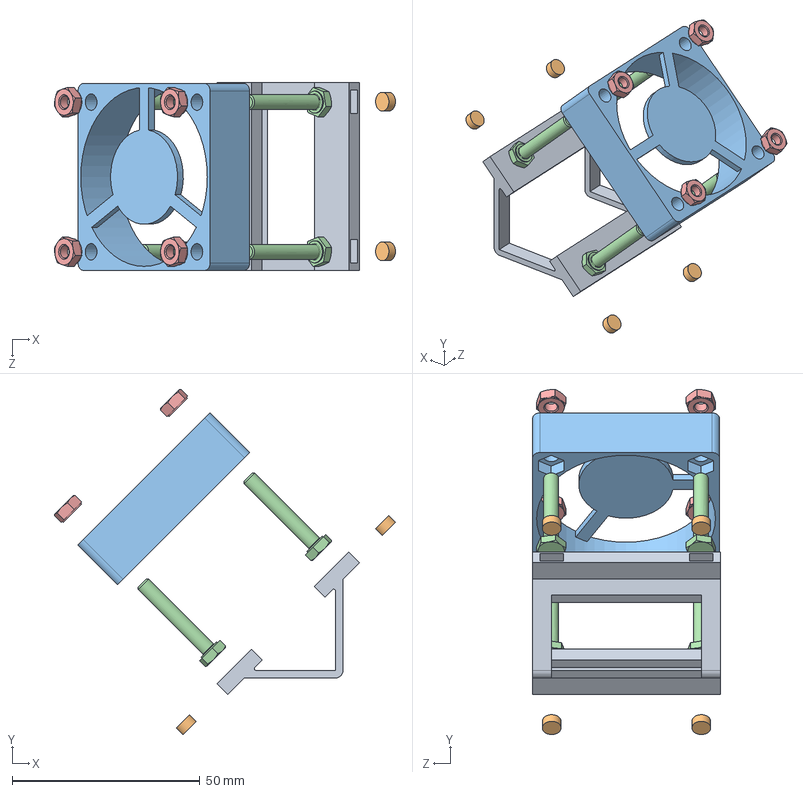
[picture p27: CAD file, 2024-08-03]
Cooling CAD/Axial Cooling/MagneticFanMountAssy.SLDASM
90.8 x 91.9 x 50.0 mm
FanBracket-V2^Cooling Assembly V3
Circular_Magnet x 4
Axial-fan
hexagon head bolt (grades a and b)_as x 4
hexagon nut style 1 (grades a and b) as x 4

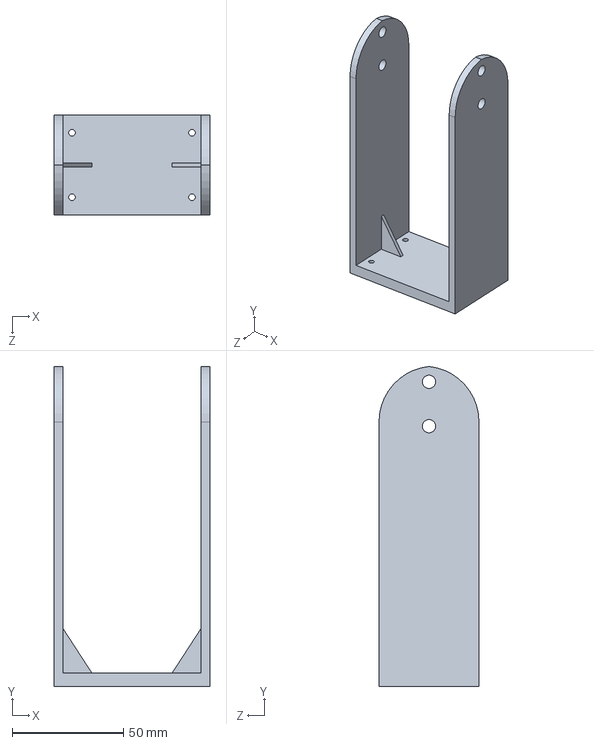
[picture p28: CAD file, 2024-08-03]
Measuring CAD/MeasurerAssyStand+Bracket.SLDPRT
70.0 x 144.0 x 45.0 mm

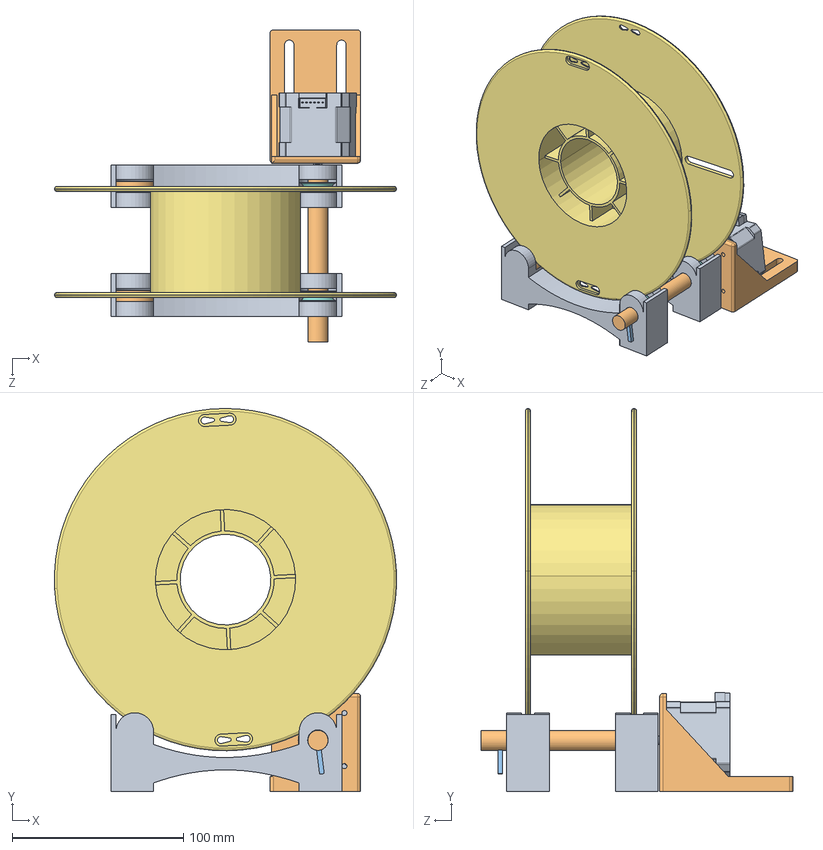
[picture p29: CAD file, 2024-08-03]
Spooling CAD/Spooling sub-assembly.SLDASM
199.9 x 223.8 x 182.5 mm
Spool Holder x 2
Shaft for motor
Ball 001.step x 2
Ball 002.step x 2
Ball 003.step x 2
Ball 004.step x 2
Ball 005.step x 2
Ball 006.step x 2
Ball 007.step x 2
Outer Ring001.step x 2
Inner Ring001.step x 2
Seal 001.step x 2
Seal 002.step x 2
Cage 001.step x 2
Cage clone 002.step x 2
Rivet 002.step x 2
Rivet 001.step x 2
Rivet 007.step x 2
Rivet 006.step x 2
Rivet 005.step x 2
Rivet 004.step x 2
Rivet 003.step x 2
esun spool
3D printed bearing ofr spooling system x 2
nema 17 model v2
Motor holder for spool
Spool shaft connector

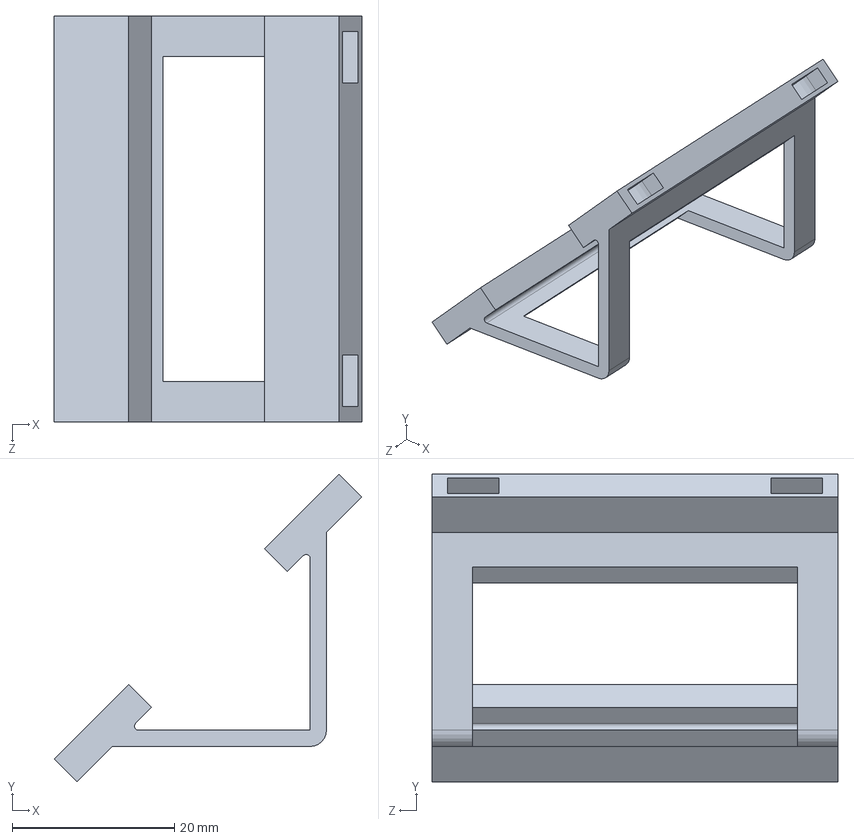
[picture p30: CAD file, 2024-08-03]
Cooling CAD/Axial Cooling/FanBracket-V2^Cooling Assembly V3.SLDPRT
37.9 x 37.9 x 50.0 mm

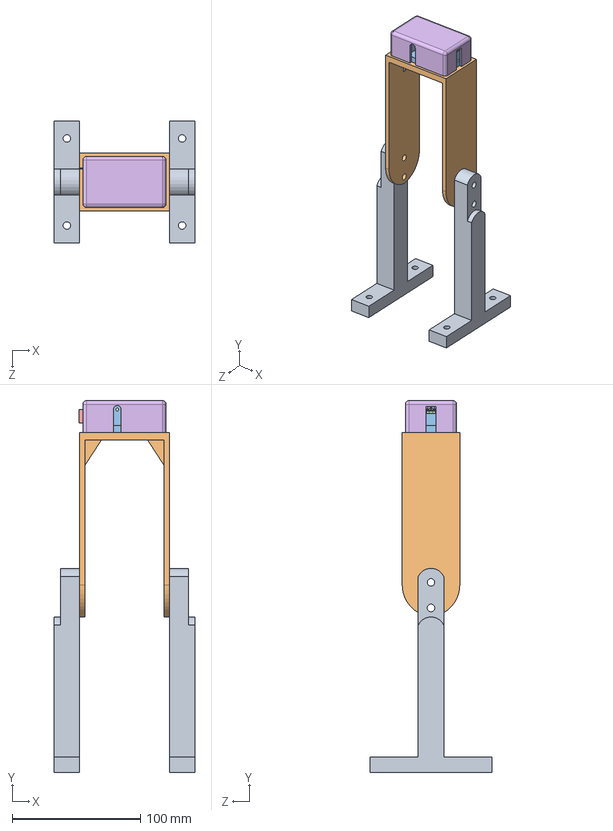
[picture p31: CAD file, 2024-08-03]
Measuring CAD/MeasuringAssy-V3.SLDASM
110.0 x 290.4 x 95.0 mm
Y-Bracket_Frame x 2
MeasurerAssyStand+Bracket
MeasuringRigBody-V3
Laser
Laser-Sensor-V2
MeasuringRigCover-V3
SiliconInsert x 2

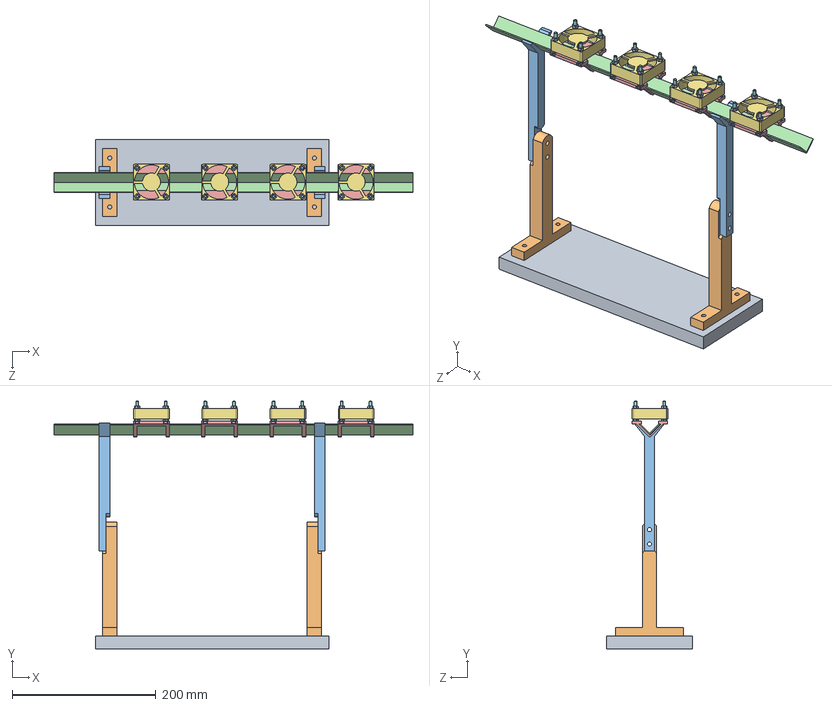
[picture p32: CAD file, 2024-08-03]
Cooling CAD/Axial Cooling/Cooling Assembly V3.SLDASM
500.0 x 344.8 x 120.0 mm
MDF-Board_Small
Y-Bracket_Frame x 2
AlExtrusion_Y-Mount x 2
20x20x1.5mm_Al-extrusion
FanBracket-V2^Cooling Assembly V3 x 4
Circular_Magnet x 16
Axial-fan x 4
hexagon head bolt (grades a and b)_as x 16
hexagon nut style 1 (grades a and b) as x 16

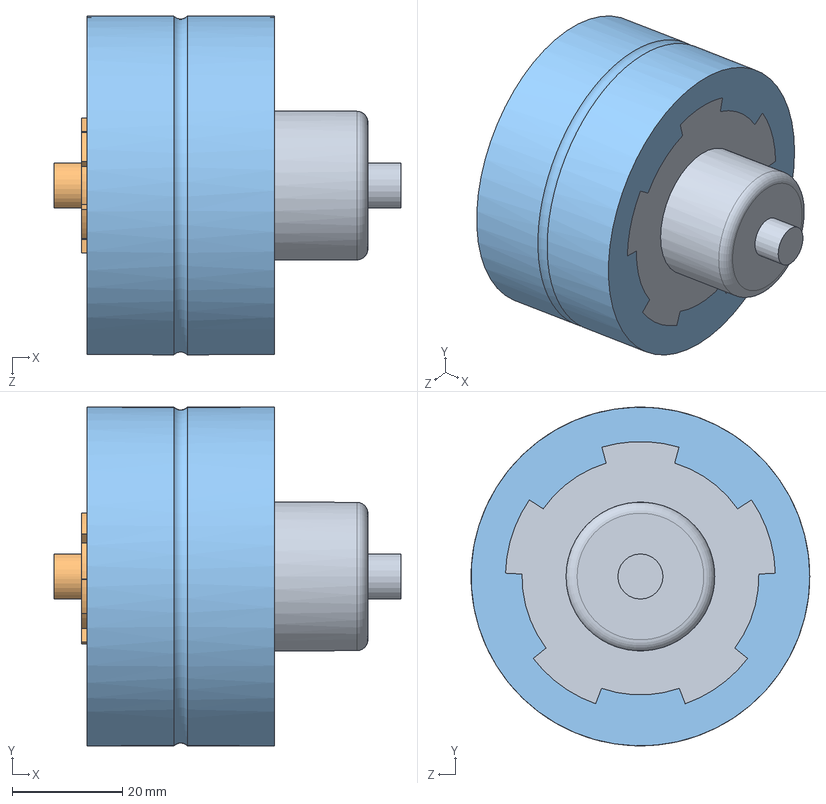
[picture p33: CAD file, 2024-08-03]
Tensioning CAD/P-V3 Roller Assembly.SLDASM
63.0 x 61.5 x 61.5 mm
P-V3 Roller Shaft
P-V3 Roller Small Shaft
P-V3 TPU Roller

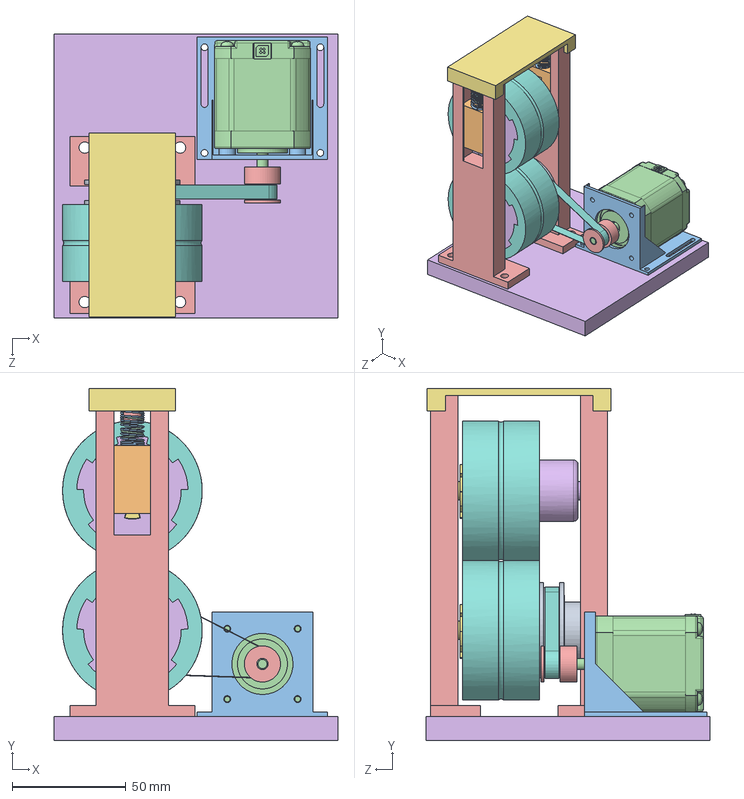
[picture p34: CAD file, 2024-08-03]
Tensioning CAD/P-V3 Stationary Bearing Assembly.SLDASM
125.0 x 155.0 x 125.0 mm
BallBearing_V1 x 4
P-V3 Bearing Housing x 2
CompSpring_V1 x 2
P-V3 Stationary Bearing Body x 2
CompSpring_V2 x 2
P-V3 Roller Shaft x 2
P-V3 Roller Small Shaft x 2
P-V3 TPU Roller x 2
GT2-60T-Pulley
P-V3 Metal Shaft for Rollers x 2
Nema17-StepperMotor Bracket
StepperMotor-MMC(6627T64)
GT2-20T-Pulley
P-V3 BasePlate
P-V3 TopCap
GT2 200mm TimingBelt

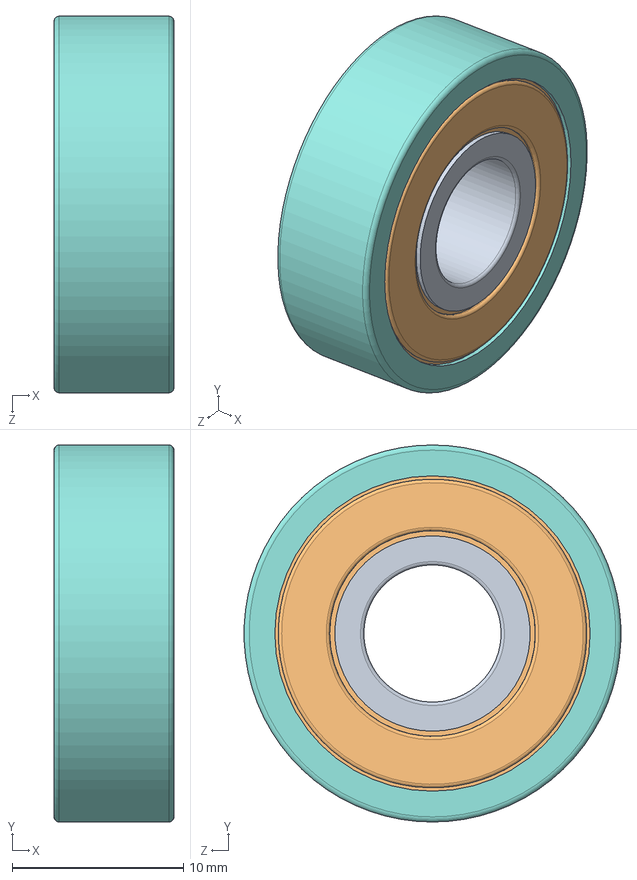
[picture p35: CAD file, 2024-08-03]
Spooling CAD/Ball Bearing 8 x 22 x 7mm.SLDASM
7.00 x 22.0 x 22.0 mm
Ball 001.step
Ball 002.step
Ball 003.step
Ball 004.step
Ball 005.step
Ball 006.step
Ball 007.step
Outer Ring001.step
Inner Ring001.step
Seal 001.step
Seal 002.step
Cage 001.step
Cage clone 002.step
Rivet 002.step
Rivet 001.step
Rivet 007.step
Rivet 006.step
Rivet 005.step
Rivet 004.step
Rivet 003.step

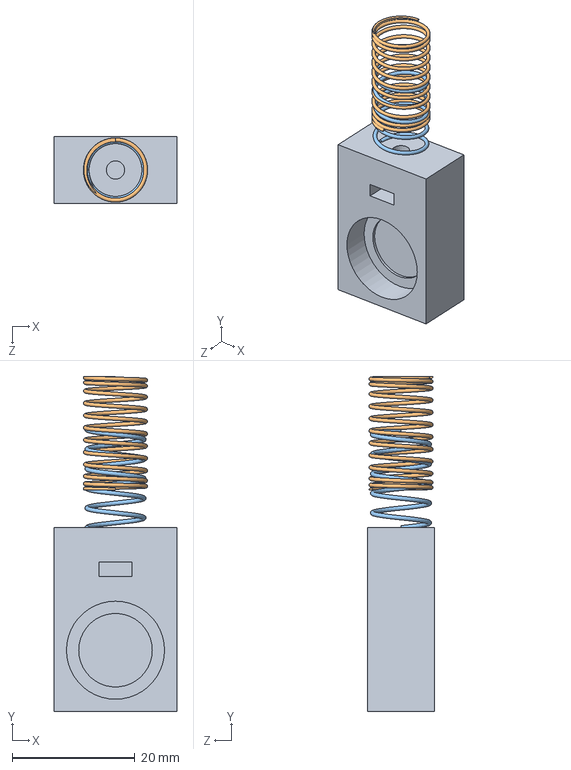
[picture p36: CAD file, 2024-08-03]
Tensioning CAD/P-V3 Bearing Housing.SLDASM
20.0 x 54.7 x 11.0 mm
P-V3 Bearing Housing
CompSpring_V1

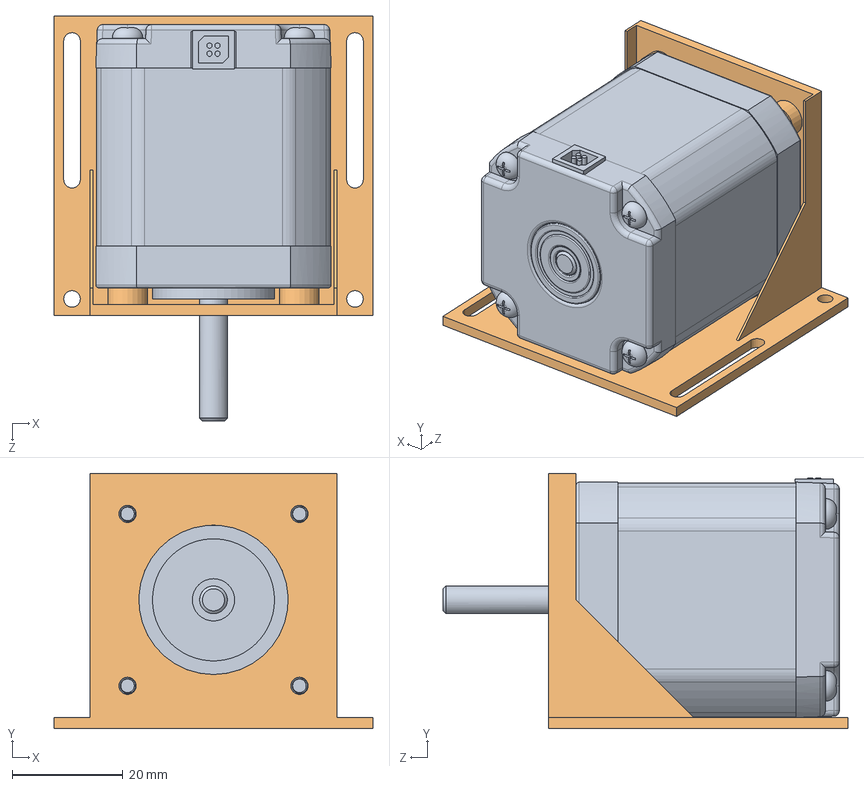
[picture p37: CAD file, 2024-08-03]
Tensioning CAD/Nema17-StepperMotor + Bracket.SLDASM
57.5 x 46.0 x 73.0 mm

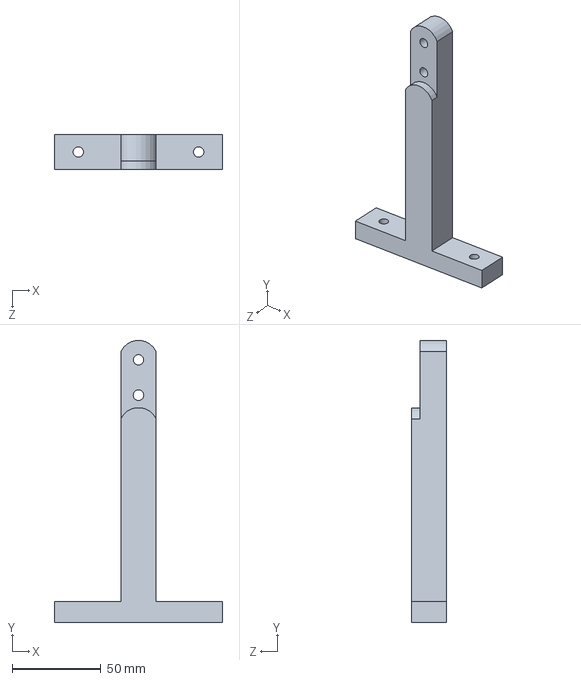
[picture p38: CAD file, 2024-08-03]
Cooling CAD/Axial Cooling/Y-Bracket_Frame.SLDPRT
95.0 x 159.3 x 20.0 mm

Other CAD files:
Measuring CAD/WoodenBase-MeasureAssy.SLDPRT
Measuring CAD/Laser.SLDPRT
Tensioning CAD/GT2 200mm TimingBelt.SLDPRT
Cooling CAD/Axial Cooling/MDF-Board_Small.SLDPRT
Cooling CAD/Axial Cooling/20x20x1.5mm_Al-extrusion.SLDPRT
Cooling CAD/Axial Cooling/AlExtrusion_Y-Mount.SLDPRT
Cooling CAD/Axial Cooling/Axial-fan.SLDPRT
Cooling CAD/Axial Cooling/Circular_Magnet.SLDPRT
Cooling CAD/Axial Cooling/Cooling Assembly V2.SLDASM
Cooling CAD/Centrifugal Cooling/Centrifugal-fan.SLDPRT
Cooling CAD/Centrifugal Cooling/CentrifugalCooling-WoodBase.SLDPRT
Cooling CAD/Centrifugal Cooling/CentrifugalFan-Base.SLDPRT
Cooling CAD/Centrifugal Cooling/CentrifugalFan-Bracket.SLDPRT
Cooling CAD/Centrifugal Cooling/CentrifugalFan-HeightArm.SLDPRT
Measuring CAD/Laser-Sensor-V2.SLDPRT
Measuring CAD/MeasuringRigBody-V3.SLDPRT
Measuring CAD/MeasuringRigCover-V3.SLDPRT
Measuring CAD/SiliconInsert.SLDPRT
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

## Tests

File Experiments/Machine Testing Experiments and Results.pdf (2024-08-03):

# Machine Testing: Experiments and Results

# P20 Filament Spoolers Autumn 2024

Project Members:
Jeremy Chu,
Mark Luu,
Duc Do,
and Jonathan Harris

P20 Filament Spoolers 2024 Autumn - DMMS

## Contents

## Introduction

The purpose of this document is to present the experiments conducted by previous groups that validates each subsystem and the overall assembly for reliability. The results gathered require initial quantitative analysis to and rigorous trial and error approach to understand the similarities between the qualitative observations compared to the theoretical assumptions.

## Recommended PPE for All Testing

- Safety glasses or some equivalent
Recommended:
- Long-sleeved shirt and pants to cover from any hazards
- Enclosed shoes always

## Cooler System

## Experiment 1: Fan Speed Measurement

To determine the speed as well as the direction of the fans across the cooling. Ideally, all fans should have relatively equal RPM to uniformly cool the filament and ensure fan ratings are receiving distributed power requirements.
Experiment 1 Apparatus:
- All Fans (Axial/Blower) required to be used for cooling
- Arduino Uno
- Cooling Trough
- Breadboard and Wires
- Laptop
- Power Supply
- Tachometer
Experiment 1 Method:
An experiment setup is demonstrated in Figure 1
1) Set up the Apparatus and power the fans to their rating requirements (Refer to Figure 1 for reference)
2) Write the code for testing and checking one fan (Refer to Figure 2 for reference)
3) Use the tachometer for record the RPM for the fan (Refer to Figure 4 for reference)
4) Repeat steps 1-3 for all other fans required for testing
5) Dependent on fan specifications, if the fan has a sensor output for RPM tracking, wire it to the Arduino and record up to ten values on the serial monitor output (Refer to Figure 3 for reference)
6) Repeat step 5 for all other fans for testing
7) Repeat Steps 1-3 where all fans are powered simultaneously
8) Record the RPM reading from all fans during simultaneous setup (Refer to Figure 4 for reference)
Experiment 1 Results:
Based on the results, testing the fans individually showed results for three out of four fans tested going beyond their specified fan RPM (> 5500 RPM). The result likely means the fan has drawn beyond its limit, caused by either significant voltage spikes (temporarily) or factor with the component itself. On the other hand, testing multiple fans in conjunction proved to show that there is linear voltage regularity amongst the fans that their speeds are within 5% tolerance. By testing the ranges from two fans in operation to four fans, it is clear that there is no significant difference between the output each fan is receiving. While the readings are given from the fans’ inherent sensors, more testing is required to validate the speed controllability. For instance, there was no available tachometer for testing with the experiment. It is recommended that testing with the tachometer is necessary to establish a comparative reading difference between the readings given by the in-built sensor of the fan and realistic observation that occurs during operation. Verifying the fan speed will clarify power distribution designed for the fans, and the necessary speed to cooling ratio such that there is efficient and managed cooling throughout the extruding operation that could cause slight, but inaccurate filament sizing.

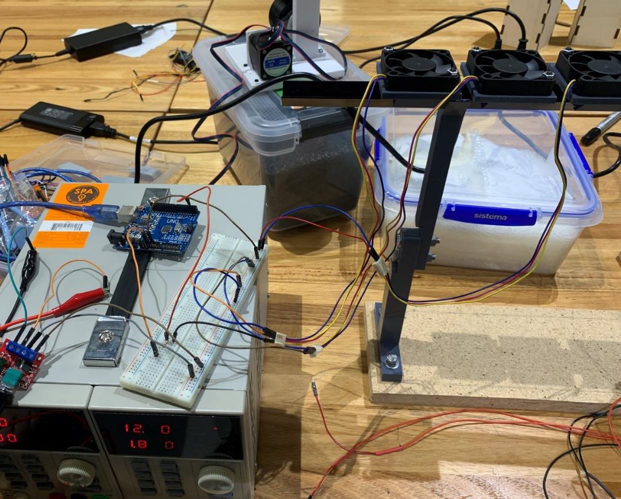
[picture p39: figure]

Figure 1: Fan Speed Experiment Setup

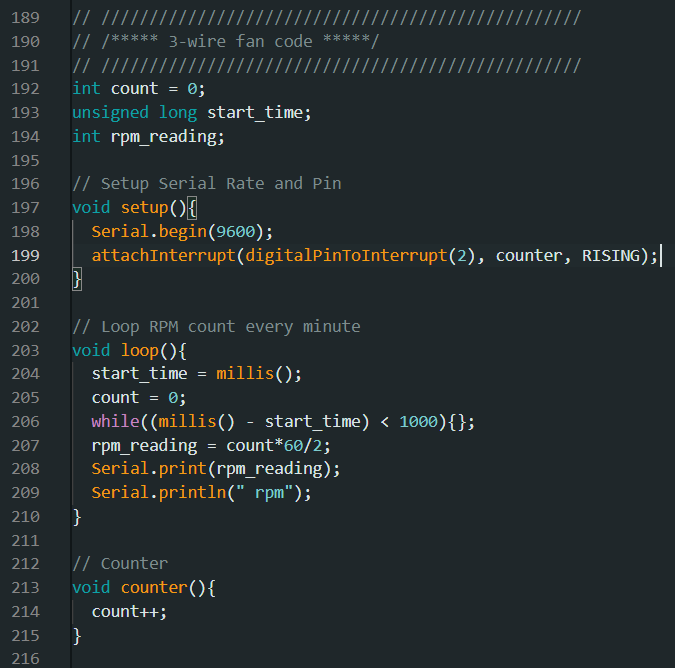
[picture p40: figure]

Figure 2: Sample Code for Fan Testing

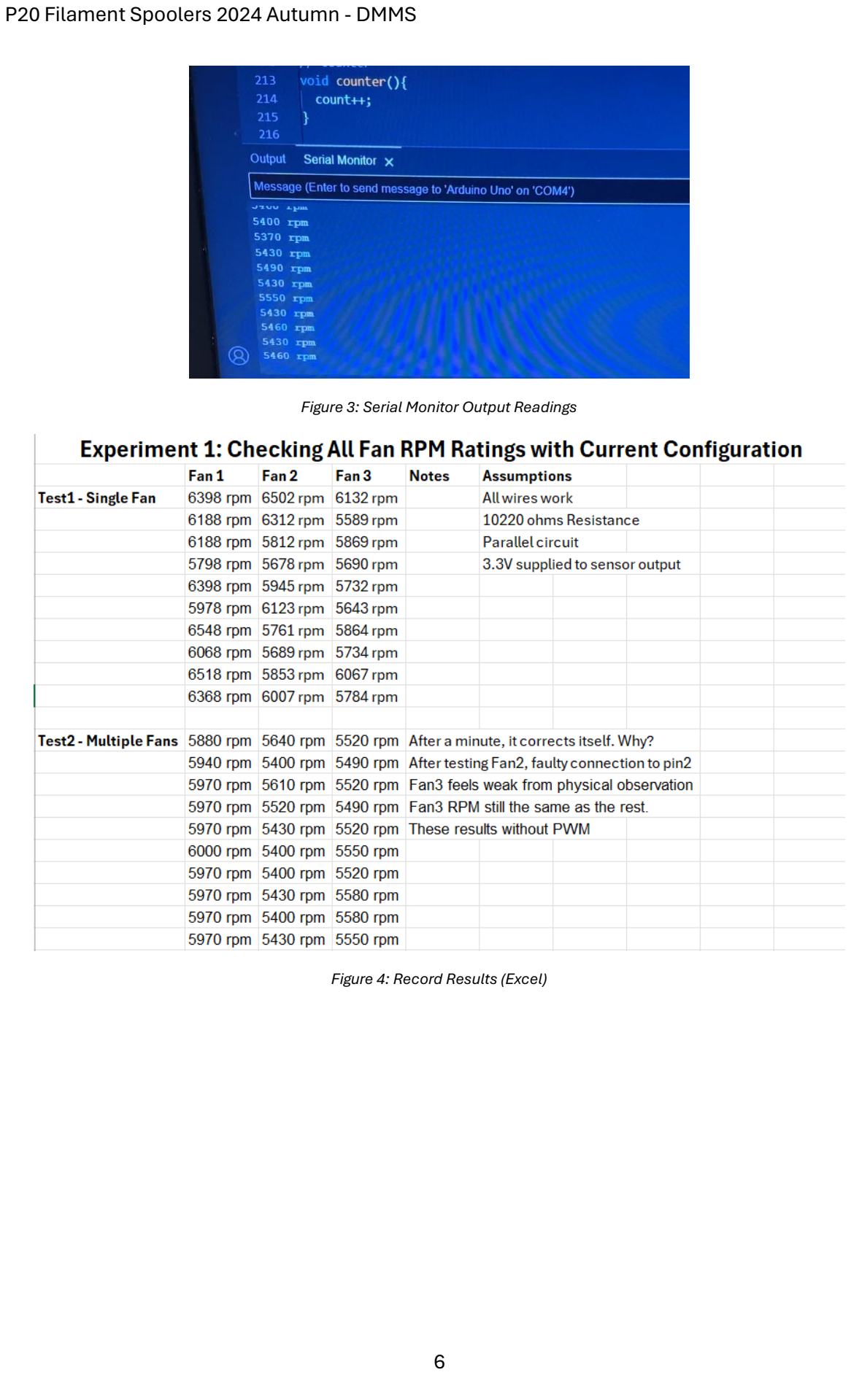
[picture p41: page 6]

Figure 3: Serial Monitor Output Readings

Figure 4: Record Results (Excel)

## Experiment 2: Cooling Layout for Filament Consistency

To determine if the cooling layout of the fans and trough minimises the expansion/shrinkage rate of the filament extruded. The purpose of the experiment is to examine the behaviour of the filament relative to the cooling setup and transferability from extruder to the tensioning subsystem. The parameters and organisation of the subsystem is vital to establish pre-defined cooling stability and ease of maintenance where cost and additional equipment is efficient. Consequently, the results of this experiment will verify enough sufficiency for the extent of air cooling required for the available extruder configurations or, if an alternative such as water/Peltier cooling should be considered.
Experiment 2 Apparatus:
- Desktop SJ35 extruder
- Fans (Axial/Blower) required to be used for cooling
- Breadboard and Wiring
- Laptop
- Filament of Choice
- Power Supply
- Cooling Trough
- Tensioning Setup
- Calliper (or equivalent filament measurer)
Experiment 2 Method:
1) Set up the Extruder settings and wait till temperatures reach desired value before commencing operation.
Extruder Settings (SJ35) (Change extruder parameters if required):
Mold Heating: 160, Barrel Heating: 130, Feed Cooling: 50, Extruder Rate: 410
2) Line up the cooling apparatus uniformly between the tensioning setup and extruder
3) Set up wiring and powering for the fans
4) Set up desired layout for testing
5) Start the extruder
6) Pull initial extruded filament till the filament is fed through the tensioner
7) Adjust tensioning speed accordingly
8) At the output end of the tensioner, cut a small sample of filament
9) Label the filament using a marker or similar distinguishing attribute
10) Stop the extruder
11)Remove all excess filament
12)Reposition the fans to change the layout of preference
13)Repeat steps 4-12 until all layouts have been analysed

Experiment 2 Results:
From the experiment, four layouts have been tested as demonstrated in Figures 5-8. The purpose of the experiment was to compare concentrated fan cooling and distributed fan cooling to identify noticeable differences in the filament quality. Layout 1 was tested equidistant along the aluminium trough, ensuring flow velocity, direction and pressure from each fan had designated areas where cooling direction was maintained. From this case, interference between cooling sections was managed for the filament to receive orderly airflow. Figure 6-8 are very similar layouts with the exception of positioning. Layout 2 was intended to be spaced equally between the extruder and tensioning to provide unaffected operation in one location whereas Layout 4 was for immediate rapid cooling and Layout 3, leaving the filament naturally elongate momentarily before the next operation. The outcomes from these layouts had small, but considerable physical differences.
Layout 1 was the most effective in filament shrinkage rate sizing at 1.8-1.85mm in diameter. This was likely due to each fan individually cooling without interference, allowing stability for the filament to deform linearly. Layout 2 had inconsistency in filament sizing ranging from 1.7-2.2mm in diameter. An identified cause was the fan closest to the extruder was slightly hot, influenced by the heat radiation of the extruder and performance of the fan will drop. This is evident, displayed by the current draw dropping on the variable power supply in testing.
Layout 3 was also inconsistent; within the first five minutes in operation, the filament was sized down to 1.5-1.6mm however, beyond that time, gradually rose to a 1.6-1.7mm range. As mentioned, this time, all fans started performing worse due to the heat. Layout 4 consequently had the opposite effect. The time difference for the filament to reach the cooling was prevalent enough that it had little impact to the filament. The filament was already deforming (~0.6-0.9) meaning, the filament was naturally shaping itself. It is also worth noting that Layouts 2-4 had high turbulent flow due to being bundled together, resulting in variation across the filament size. These results provide preliminary understanding of the cooling subsystem architecture. Small discrepancies and layout decision will be required to be factored into consideration to meet consistency and desired filament diameter. There are two unaccounted testing that also need to be analysed. Only two materials have been tested: PLA and flexi ABS. More recyclable material can introduce unexpected outcomes; therefore, layout could depend on material. With this hypothetical aspect, the second factor is having a more modular layout that can be adjusted in respect to the material, relative subsystems and the extruder settings.

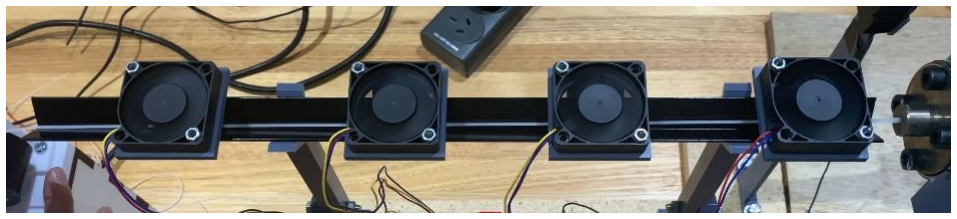
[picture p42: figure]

Figure 5: Layout 1 – Equidistant Fan Layout

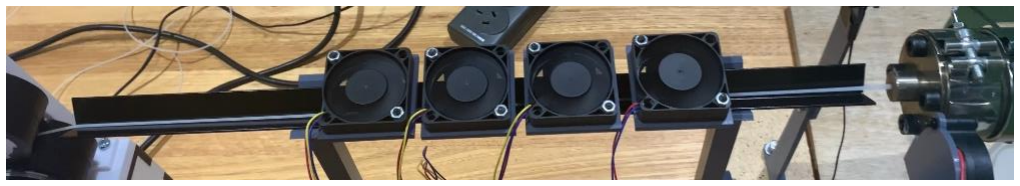
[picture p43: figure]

Figure 6: Layout 2 – Middle Section Focus

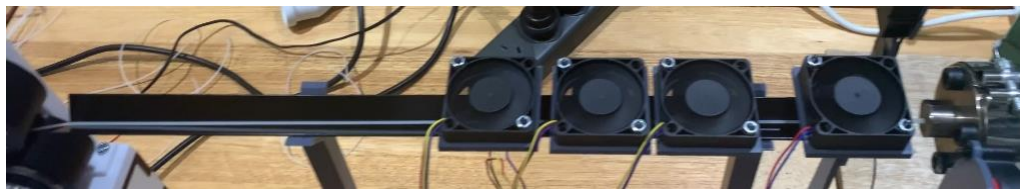
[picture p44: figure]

Figure 7: Layout 3 – Extruder Nozzle Focus

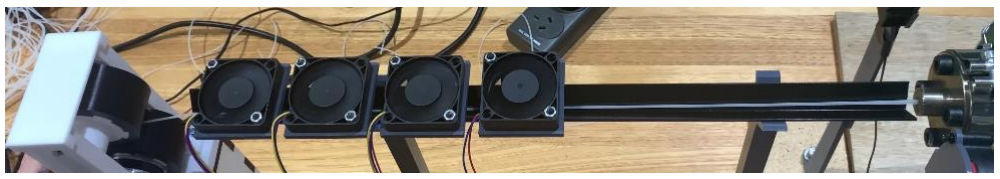
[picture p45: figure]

Figure 8: Layout 4 – Cooling relative to Tensioning Subsystem

## Experiment 3: Temperature Controllability with Extruder Configurations

To determine the temperature changes across the cooling subsystem. The objective of the experiment is to determine the temperature changes between fan cooling across the overall cooling subsystem. Clarifying the experimental results of the temperature changes relative to a preliminary heat transfer analysis of the subsystem will improve the validation of temperature control and optimising the control quality of the filament.
Experiment 3 Apparatus:
- Desktop SJ35 extruder
- Number of Fans (Axial/Blower) required to be used for cooling
- Arduino Uno
- Breadboard and Wires
- Laptop
- Cooling setup ready
- Temperature Gun
- Tensioning Setup
Experiment 3 Method:
1) Set up the Extruder settings and wait till temperatures reach desired value before commencing operation.
Extruder Settings (SJ35) (Change extruder parameters if required):
Mold Heating: 160, Barrel Heating: 130, Feed Cooling: 50, Extruder Rate: 410
2) Line up the cooling apparatus uniformly between the tensioning setup and extruder
3) Set up wiring and powering for the fans
4) Set up desired layout for testing
5) Start the extruder
6) Pull initial extruded filament till the filament is fed through the tensioner
7) Adjust tensioning speed accordingly
8) Use Layout 1 (Refer to Figure 5) to ensure the fans
9) Measure the temperature reading in close and safe proximity to the measured fan 10)Record the reading of the temperature gun (Refer to Figure 9 for reference)
11) Stop the extruder upon recording results
12)Repeat step 9 with all other fans during operation
13)Repeat steps with different fan layout (Refer to Figure 6-8)
Experiment 3 Results:
Upon collecting results, there is variation between temperatures. Taking readings at approximate 0.05, 0.1 and 0.15m away from each fan, the temperature drops were not found linear. It is also difficult to determine the actual temperature upon extrusion as the temperature gun cannot measure off reflective surfaces. Although there is a reference temperature via the extruder settings, it is still unclear as to whether the extruder values are true output values as per in operation. Unfortunately, not enough tabulated data has been collected for this experiment due to time constraints and accessibility to use measuring tools outside of the UTS Protospace facility. Figure 10 is provided for a sample layout in data and part information for calculations. However, it is advised that for improvements concerning the temperature management of the cooling subsystem, that both a heat transfer paper analysis to experimental observation is researched to understand the outcomes of heat dissipation. Furthermore, this concept can introduce temperature control where the cooling system operation correlates to the temperature of the filament, self-adjusting until the diameter from the measurer is maintained.

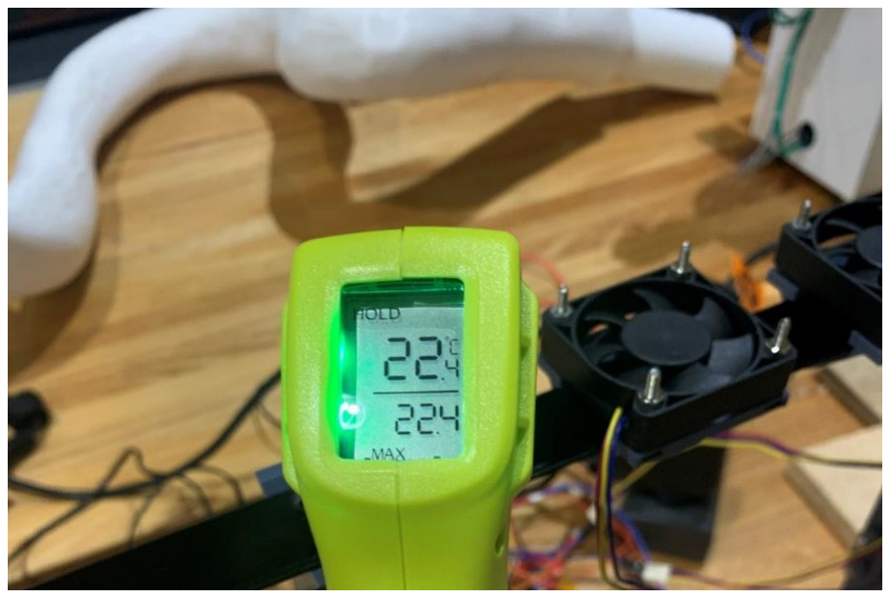
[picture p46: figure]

Figure 9: Temperature Gun Reading

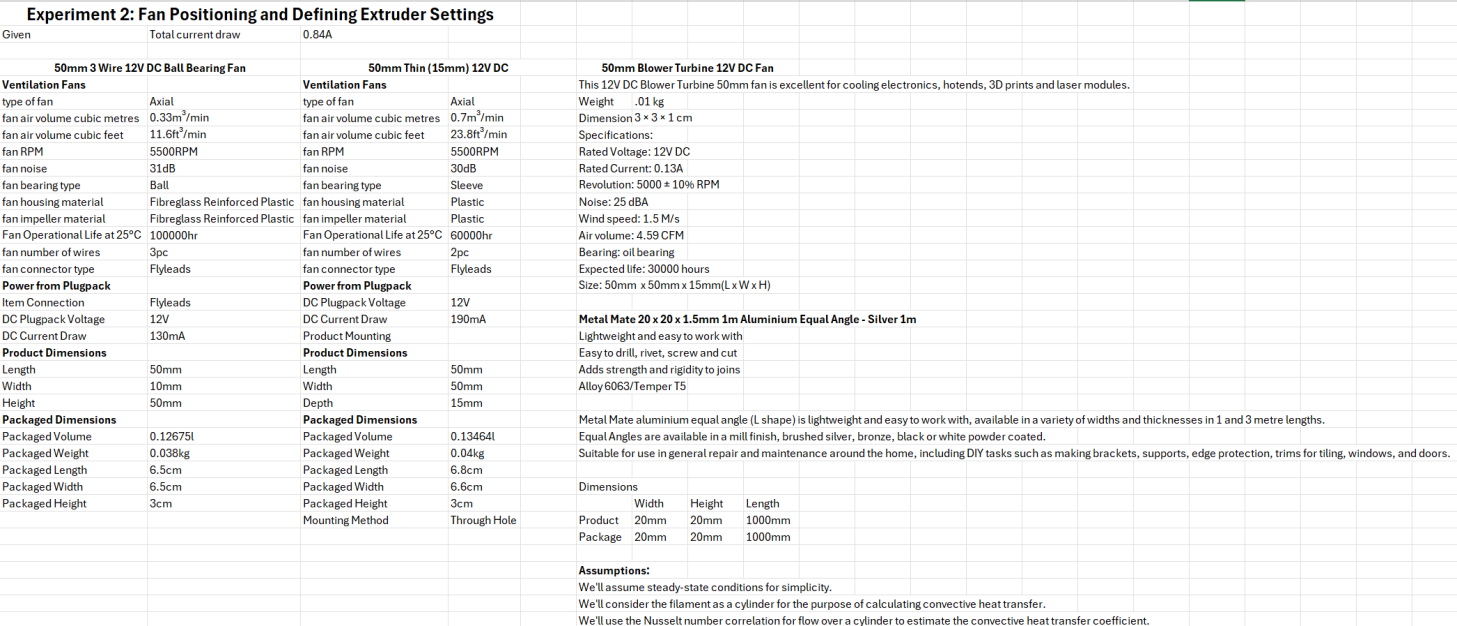
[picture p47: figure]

Figure 10: Preliminary Heat Transfer Analysis and Part Parameters

## Measuring System

## Experiment 1: Consistent Accurate Readings for Different Material

To ensure the consistency and accuracy of light measurements from the laser and the light intensity sensor, it is essential to test the system using freshly made filaments. However, we will use filaments that is premade and pulled through the measurement systems as this provided a controlled environment to assess how well the laser's light interacts with the filament material. This testing is essential to verify that the laser and light sensor accuracy while maintains its specified performance criteria, such as the wavelength and power output, when interacting with different materials, thereby ensuring reliable and precise readings.
Experiment 1 Apparatus:
- 60cm of different filaments (PLA, ABS)
- Laser pointer
- Light Sensitivity Sensor
Experiment 1 Method:
1. Arrange the experimental setup as illustrated in Figure 12. Ensure all components are correctly positioned and securely mounted.
2. Set up the code as shown in Figure 13. Ensure that all parameters are accurately inputted, and that the library is fully UpToDate.
3. Gently pull the premade filament through the designated opening in the setup, ensuring the laser directly hits the filament. This alignment is crucial for accurate data capture.
4. Record the data as the filament interacts with the laser. Ensure that the data acquisition system is properly calibrated and running smoothly to capture accurate readings.
5. Repeat steps 2 and 3 for each type of filament.

Experiment 1 Results:

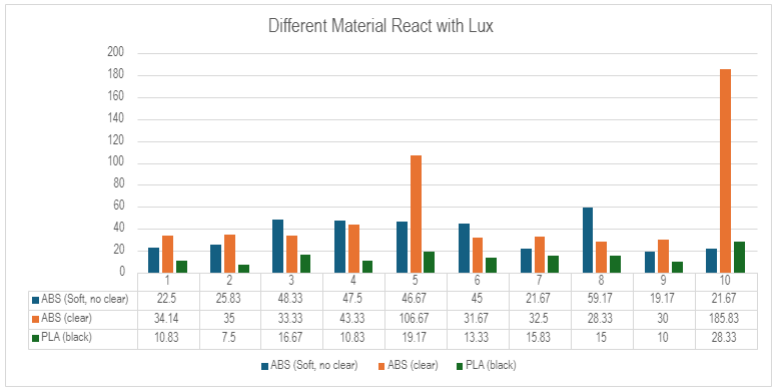
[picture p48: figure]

Figure 11. Results of experiment 1
Based on the result of the graph above, there is a clear different in the light reading as different materials property corresponded to different light levels. The three materials that were used are ABS-clear, soft and non-clear as well as PLA which all have different density and properties. From the experiment conducted, we can see the clear ABS have the highest reading of all which is around 30 lux. This is due to its property which means materials with higher transparency allow more light to pass through more. This cause the reading to be higher when comparing with other materials.
When looking at the reading for the other materials, like non-clear ABS and PLA, they have denser property which make them less transparency. Therefore, making them have a low reading then the clear ABS of 21.67 lux for non-clear ABS and 15 lux for PLA. This verified how material parameters are greatly affecting the light intensity measurement by the density, material property and the transmission capabilities. Therefore, we recommend testing different material first and getting the parameters for accurate measurement.


Figure 12: Laser-sensor setup

Figure 13: Laser-sensor Arduino coding


Figure 14: Lux Output Measurement

## Experiment 2: Consistent Accurate Readings for Different Diameters

To evaluate the consistency and accuracy of light measurements from a laser as it interacts with filament of varying diameters. The experiment used the same type of material PLA but with two specific diameters: 1.75mm and 2.88mm. These filaments are premade so there will be no filament error when testing. These filaments will be guided slowly through the system, a method designed to ensure precision in capturing data. This controlled pace allows for the accurate assessment of how different filament thicknesses affect the transmission of laser light. Furthermore, we can use these data to convert the lux measurement to millimetres for the filament diameters which will be used for the freshly made filament.
Experiment 2 Apparatus:
- 60cm of different diameters filament, PLA (1.75 & 2.88)
- Laser pointer
- Light Sensitivity Sensor
Experiment 2 Method:
1. Arrange the experimental setup as illustrated in Figure 12. Ensure all components are correctly positioned and securely mounted.
2. Set up the code as shown in Figure 13. Ensure that all parameters are accurately inputted, and that the library is fully UpToDate.
3. Gently pull the premade filament through the designated opening in the setup, ensuring the laser directly hits the filament. This alignment is crucial for accurate data capture.
4. Record the data as the filament interacts with the laser. Ensure that the data acquisition system is properly calibrated and running smoothly to capture accurate readings.
5. Repeat steps 2 and 3 for each diameter of filament.

Experiment 2 Results:


Figure 15. Results of experiment 2
When conducting tests on PLA filaments with different diameters, it is seen that the filament thickness significantly influences the light intensity measurements. As when looking at the graph we can see the 1.75mm filament diameters shown an average lux of around 8.33 lux while the 2.88mm filament produce a lower measurement of 5.83 lux. This decrease in lux measurement shown how the thickness of the diameters block light from passing through and making the sensor from picking up the full measurement. Therefore, based on these data we can convert this measurement from lux to millimetres. However, we were unable to make the equation work for the filament as there were too much mix data when materials are place through which create an incorrect reading which make the equation become ineffective. Note: In the graph, there is a sudden increase in the reading which is due to the filament having deformed or eaten through which cause it to misshape and creating these errors. (figure 15)


Figure 16: Deformed filament, not good for testing.

## Experiment 3: Consistent Accurate Readings with Different Positioning

To determine the consistency and accuracy of the light measurement when changing the filament's position in relation to the laser and the sensor will impact the stability of the measurement reading. In the setup, the filament will be positioned to move either in the middle or close to either the laser or the sensor to determine at which location does it produce the most accurate reading. Furthermore, we can use this data to redesign the system to get the most accurate reading.
Experiment 3 Apparatus:
- 60cm of PLA filament
- Laser pointer
- Light Sensitivity Sensor
Experiment 3 Method:
1. Arrange the experimental setup as illustrated in Figure 12. Ensure all components are correctly positioned and securely mounted.
2. Set up the code as shown in Figure 13. Ensure that all parameters are accurately inputted, and that the library is fully UpToDate.
3. Gently pull the premade filament through the designated opening in the setup, ensuring the laser directly hits the filament. This alignment is crucial for accurate data capture.
4. Record the data as the filament interacts with the laser. Ensure that the data acquisition system is properly calibrated and running smoothly to capture accurate readings.
4. Repeat steps 2 and 3 for each position of filament.

Experiment 3 Results:


Figure 17. Shows the results of experiment 3
In assessing the optimal positioning of filament relative to their interaction with the sensor, three distinct locations were tested: close to the sensor, close to the laser, and in the middle between both. Base on the data taken, its shown that the position closer to the laser and the middle seem to produce the most sustainable reading while closer to the sensor produce a unstable reading. This is due to the light reflecting on the filament which depending on the position will create different result. Therefore, if it's close to the sensor it will block the light which make the result become in accurate. So, based on this result, we have setup the filament to be close to the laser for more accurate reading.

## Tensioning System

Unless stated otherwise:

- Left heating: 150*C
- Middle heating: 140*C
- Right heating: 50*C
- Extrusion rate = 410 gauge

## Experiment 1: Is the Pulling Action of the Motor Sufficient for Tensioning?

To test whether the pulling action of the rollers is sufficient, freshly extruded but cooled filament (mystery 1588ATL) will be placed inside of the rollers. Filament in the tensioner should be relatively difficult to pull out when tugged but also remain in its circular shape previous to the tensioning. This is a qualitative experiment.
Experiment 1 Apparatus:
- Desktop SJ35 extruder
- Cooling and Tensioning assemblies
- 300g of dried ABS plastic pellets
- Metal spatula
- Pliers
Experiment 1 Method:
An experimental setup can be seen in figure 21.
1) Heat the extruding device to temperatures suitable for the extrusion of ABS plastic.
2) Once heated, run the system to extrude material from previous uses, use a high speed setting (e.g., >800 gauge (8.7 RPM)).
3) After previous material has been removed from the system, place about 150-300g of ABS plastic pellets into the hopper.
4) Run the system again on a high setting until the filament extruded is consistent – this step is to remove any other residue not previous vacated, have a metal spatula ready to catch freshly extruded material should it misguide itself or splatter.
5) Turn on the cooling and tensioning assemblies.
6) Extrude the material using a speed of 2.97 RPM (220 gauge) and use pliers to pass it through the cooling system. Should the microstepping mode change or you wish to use a different gauge setting, refer to the Excel sheet “Stepper motor calculations for code” as can be pictured in figure 22.
7) Parse the filament through the rollers of the tensioning device, this will be running at a speed of 4 RPM (myStepper.setSpeed(400) using full microstepping).
8) Wait until filament diameter stabilises, IF:

a. The filament breaks, lower the tensioning speed (e.g., to 2.5 RPM (myStepper.setSpeed(250))).
b. The filament is too large or tangles, increase the tensioning speed (to 6 RPM (myStepper.setSpeed(600))).
9) Once diameter has stabilised, observe action of the rollers and filament passing and record observation.
Experiment 1 Results:
Here, figure 18. shows a control sample (bottom) and an increased tensioning sample (top) of material extruded. It can be observed that the filament with increased speed applied to the tensioner is of a smaller diameter. Figure 19. demonstrates this thinning effect displaying the test length decreasing as speed of the tensioner increases with smaller a diameter of the inside spiral length representing increased speed. When the speed of the tensioner was reduced however the filament began to significantly deform and curve (see fig. 20). This is explainable as filament is being extruded quicker than it can be pull, resulting in slack.


Figure 18. | Figure 19.

An unexpected result from this experiment were undesirable geometric artefacts. As can be seen in Figure 18 and 20., the filament extruded has an uneven surface of pattern-like sharp increases and decreases of diameter. The suspect for this is the physical action of the stepper motor actuating steps using the full microstepping mode. In this case, a full microstepping mode would mean that each angular step is relatively large (1.8°), resulting in noticeable vibration and jagged motion of the drive shaft. As such, a smaller microstepping mode which would divide these large angular steps into smaller increments, should in theory allow for smoother motion and reduced vibration. This was later verified in Experiment 2 which used a 1/16 microstepping mode with noticeable improvements in filament consistency (see fig. 23.)


Figure 20.

Figure 21. Shows the experimental set up of tensioning experiments 1 and 2. From right to left displays the extruder, the cooling assembly, and tensioning assembly.


Figure 22. Shows the relationship between the extruder’s gauge reading to the actual RPM values produced. A linear pattern is observed.
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

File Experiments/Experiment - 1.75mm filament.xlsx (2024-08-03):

EXTRUDER PARAMETERS
Speeding | 410
Left: | 150
Middle | 130
Right | 50
TEST: Filament Diameters per RPM
 | RPM
 | 8 | 8.5 | 9 | 9.5 | 10 | 10.5 | 11 | 11.5 | 12 | 12.5 | 13
Measurement 1 | 1.92 | 1.95 | 1.88 | 1.83 | 1.73 | 1.61 | na
Measurement 2 | 1.92 | 1.88 | 1.9 | 1.84 | 1.72 | 1.57
Measurement 3 | 1.88 | 1.92 | 1.85 | 1.84 | 1.73 | 1.58
Measurement 4 | 1.93 | 1.9 | 1.87 | 1.81 | 1.71 | 1.6
Measurement 5 | 1.94 | 1.88 | 1.88 | 1.82 | 1.71 | 1.6
Average
ROLLER RPM TO ARDUINO SPEED CHART
1/16 Microstepping - 1.8* Stride GearRatio=1:3, 9600 pulses/rev
RPM Wanted | 10 | 10.5 | 11 | 11.5 | 12 | 12.5 | 13
Arduino Equivalent | 48000 | 50400 | 52800 | 55200 | 57600 | 60000 | 62400
 | 96000 | 100800 | 105600 | 110400 | 115200 | 120000 | 124800
 | 10.5 | 10.6 | 10.7 | 10.8 | 10.9 | 11
TEST: Filament Diameters per RPM
 | RPM
 | 9.5 | 9.6 | 9.7 | 9.8 | 9.9 | 10
Measurement 1 |  |  |  |  | 1.74 | 1.73
Measurement 2 |  |  |  |  | 1.74 | 1.72
Measurement 3 |  |  |  |  | 1.82 | 1.73
Measurement 4 |  |  |  |  | 1.71 | 1.71
Measurement 5 |  |  |  |  | 1.79 | 1.71
Average

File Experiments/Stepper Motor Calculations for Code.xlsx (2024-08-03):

VARIABLES
Pulse Ratio: |  | 3.00
Stride angle: |  | 1.80
Microstepping mode: | One-sixteenth | 0.0625
RESULTS
Actual Pulse-to-Angle ratio |  | 0.04 | deg/pulse
Steps for a full revolution: |  | 9600.00 | pulses/rev
STEPPER MOTOR PARAMETERS FOR ARDUINO
I want to:
Perform x amount of revolutions | x: | 1.25 | "steps" required: | 12000
X RPM | x: | 5.00 | "speed" value: | 8000
Gear Ratio: 20:50 | 3.00
Roller Revolutions wanted | x: | 1.00
 | Stepper Revs req'd: | 3.00 | "steps" required: | 28800
Roller RPM wanted | X: | 7.00
 | Stepper RPM req'd: | 21.00 | "speed" value: | 33600
DESKTOP SJ35 PARAMETERS
Wanted RPM | 11.00
Gauge Reading Req'd | 824.0902256
Wanted Gauge Reading | 1120.00
Equivalent RPM | 14.94
LINEAR EXTRUSION RATE FOR IDEAL CONDITIONS
Linear extursion rate = RPM*circumference = X mm/min
Linear extrusion rate: | 0.00 |  | Roller Diameter:
Total extruded length = Revs * circumference |  |  | Roller Circumference:
Total extruded length: | 0.00
MICROSTEPPING MODES (DO NOT TOUCH)
Step |  | MS1 | MS2 | MS3
Full | 1.0000 | L | L | L
Half | 0.5000 | H | L | L
Quarter | 0.2500 | L | H | L
One-eighth | 0.1250 | H | H | L
One-sixteenth | 0.0625 | H | H | H

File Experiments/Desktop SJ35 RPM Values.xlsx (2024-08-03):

Table X: Experimental Data of seconds/rev and Results of RPM
Gauge | 120 | 200 | 300 | 400 | 500 | 600 | 700 | 800 | 900 | 1000 | 1100 | 1200 | 1300
Test 1 (s/rev) | 37.83 | 22.41 | 14.93 | 11.22 | 8.90 | 7.45 | 6.34 | 5.71 | 4.97 | 4.53 | 4.05 | 3.72 | 3.46
Test 2 (s/rev) | 37.94 | 22.32 | 14.91 | 11.10 | 8.93 | 7.46 | 6.41 | 5.58 | 5.07 | 4.47 | 4.06 | 3.73 | 3.47
Test 3 (s/rev) | 37.83 | 22.32 | 14.92 | 11.19 | 8.98 | 7.46 | 6.45 | 5.55 | 5.02 | 4.51 | 4.13 | 3.79 | 3.51
Average | 37.87 | 22.35 | 14.92 | 11.17 | 8.94 | 7.46 | 6.40 | 5.61 | 5.02 | 4.50 | 4.08 | 3.75 | 3.48
RPM | 1.58 | 2.68 | 4.02 | 5.37 | 6.71 | 8.05 | 9.38 | 10.69 | 11.95 | 13.32 | 14.71 | 16.01 | 17.24
RPM CALCULATOR
Wanted RPM | 13
Gauge Req'd | 974.4661654
Gauge Reading
Equivalent RPM

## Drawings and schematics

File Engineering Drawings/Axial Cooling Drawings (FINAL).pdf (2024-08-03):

# Engineering Drawings for:

# Axial Cooling

# Filament Spooling Team

## University of Technology Sydney

## for 43019 Design in Mechanical and Mechatronic Systems - Autumn 2024

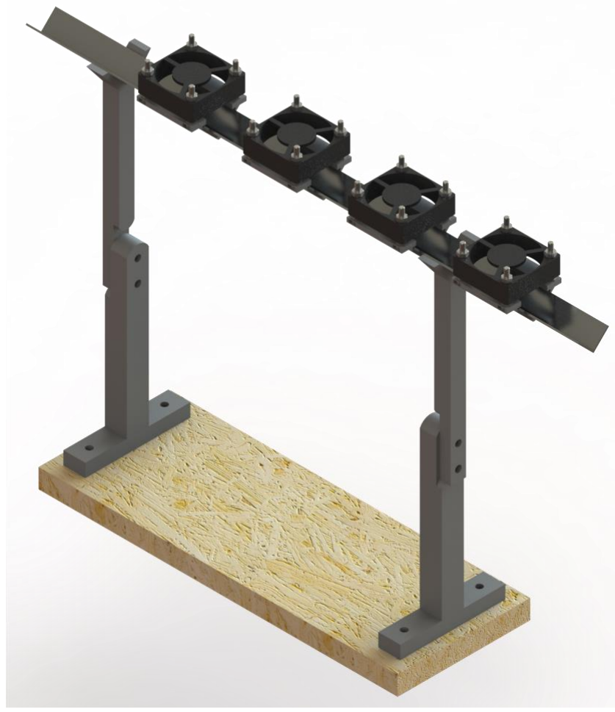
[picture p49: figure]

# Design and Drawings: Jeremy Chu

Cooling Assembly V3 | 2
MagneticFanMountAssy | 3
Y-Bracket_Frame | 4
AlExtrusion_Y-Mount | 5
FanBracket-V2^Cooling Assembly V3 | 6
20x20x1.5mm_Al-extrusion | 7
MDF-Board_Small | 8

4
5.5

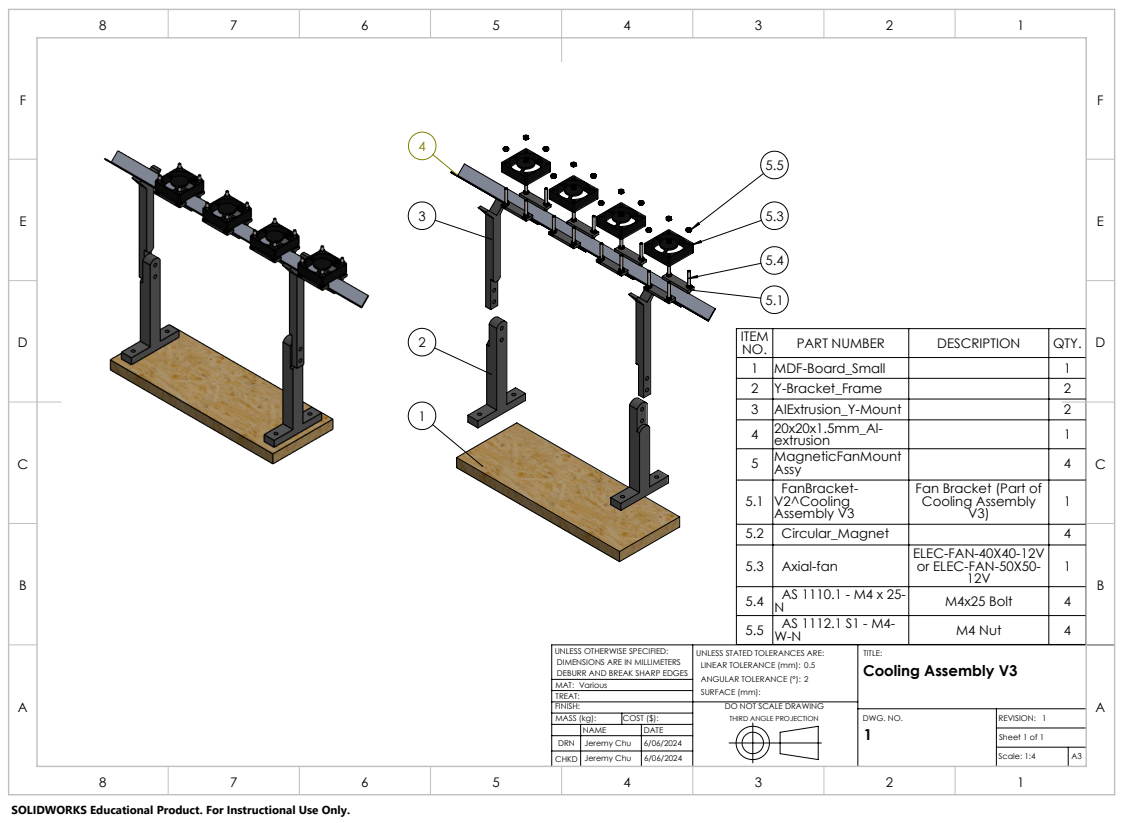
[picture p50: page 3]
Circular_Magnet; MAT: TREAT:; DWG. NO.; REVISION:; Sheet 1 of 1; Various

ITEM NO. | PART NUMBER | DESCRIPTION | QTY.
1 | MDF-Board_Small | | 1
2 | Y-Bracket_Frame | | 2
3 | AlExtrusion_Y-Mount | | 2
4 | 20x20x1.5mm_Al-extrusion | | 1
5 | MagneticFanMount Assy | | 4
5.1 | FanBracket-V2^Cooling Assembly V3 | Fan Bracket (Part of Cooling Assembly V3) | 1

5.3 | Axial-fan | ELEC-FAN-40X40-12V or ELEC-FAN-50X50-12V | 1

5.4 | AS 1110.1 - M4 x 25-N | M4x25 Bolt | 4
5.5 | AS 1112.1 S1 - M4-W-N | M4 Nut | 4

UNLESS OTHERWISE SPECIFIED: DIMENSIONS ARE IN MILLIMETERS DEBURR AND BREAK SHARP EDGES | UNLESS STATED TOLERANCES ARE: LINEAR TOLERANCE (mm): 2 0.5 ANGULAR TOLERANCE (°): SURFACE (mm): | TITLE: Cooling Assembly V3

FINISH: | DO NOT SCALE DRAWING THIRD ANGLE PROJECTION
MASS (kg): | COST ($):
NAME | DATE
DRN | Jeremy Chu | 6/06/2024
CHKD | Jeremy Chu

Scale: 1:4 | A3

SOLIDWORKS Educational Product. For Instructional Use Only.

5

F | F

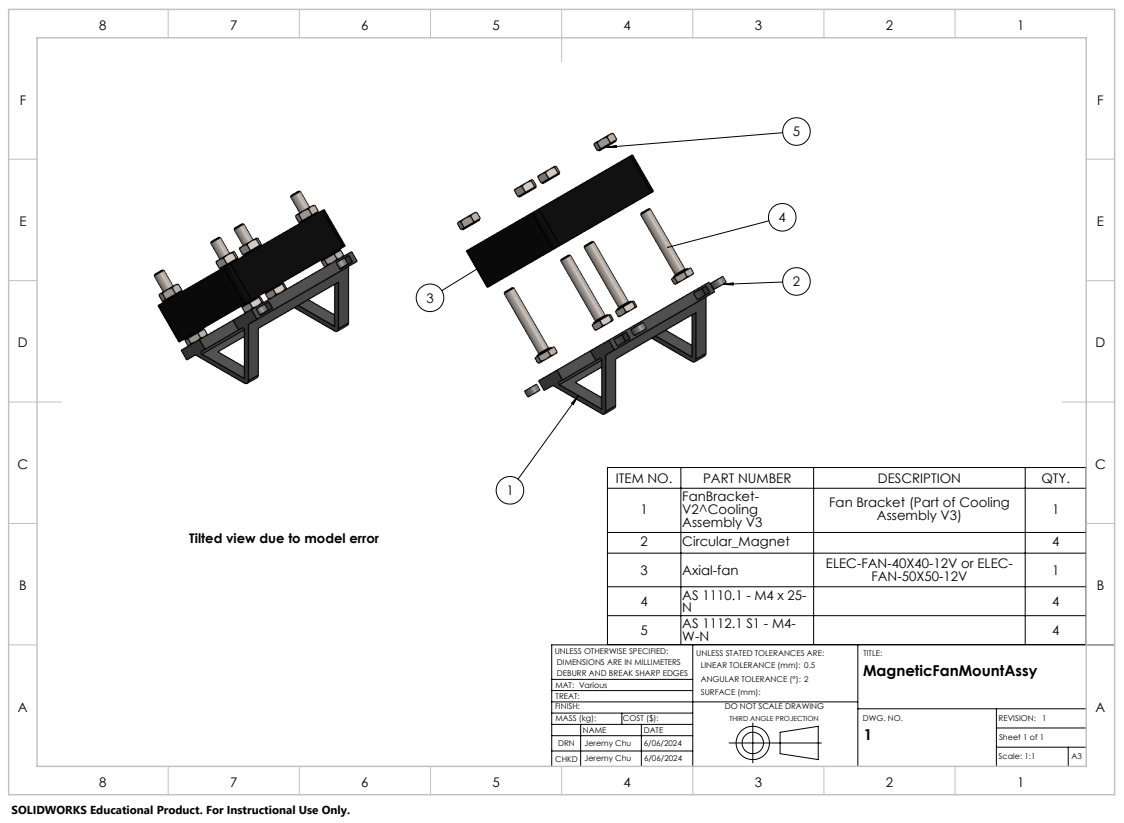
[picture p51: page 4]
MAT: TREAT:; DWG. NO.; REVISION:; Sheet 1 of 1; Scale: 1:1; Various

ITEM NO. | PART NUMBER | DESCRIPTION | QTY.
1 | FanBracket-V2^Cooling Assembly V3 | Fan Bracket (Part of Cooling Assembly V3) | 1

Tilted view due to model error

2 | Circular_Magnet | | 4
3 | Axial-fan | ELEC-FAN-40X40-12V or ELEC-FAN-50X50-12V | 1
4 | AS 1110.1 - M4 x 25-N | | 4
5 | AS 1112.1 S1 - M4-W-N | | 4

UNLESS OTHERWISE SPECIFIED: DIMENSIONS ARE IN MILLIMETERS DEBURR AND BREAK SHARP EDGES | UNLESS STATED TOLERANCES ARE: LINEAR TOLERANCE (mm): 2 0.5 ANGULAR TOLERANCE (°): SURFACE (mm): | TITLE: MagneticFanMountAssy

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

34.00
F | F

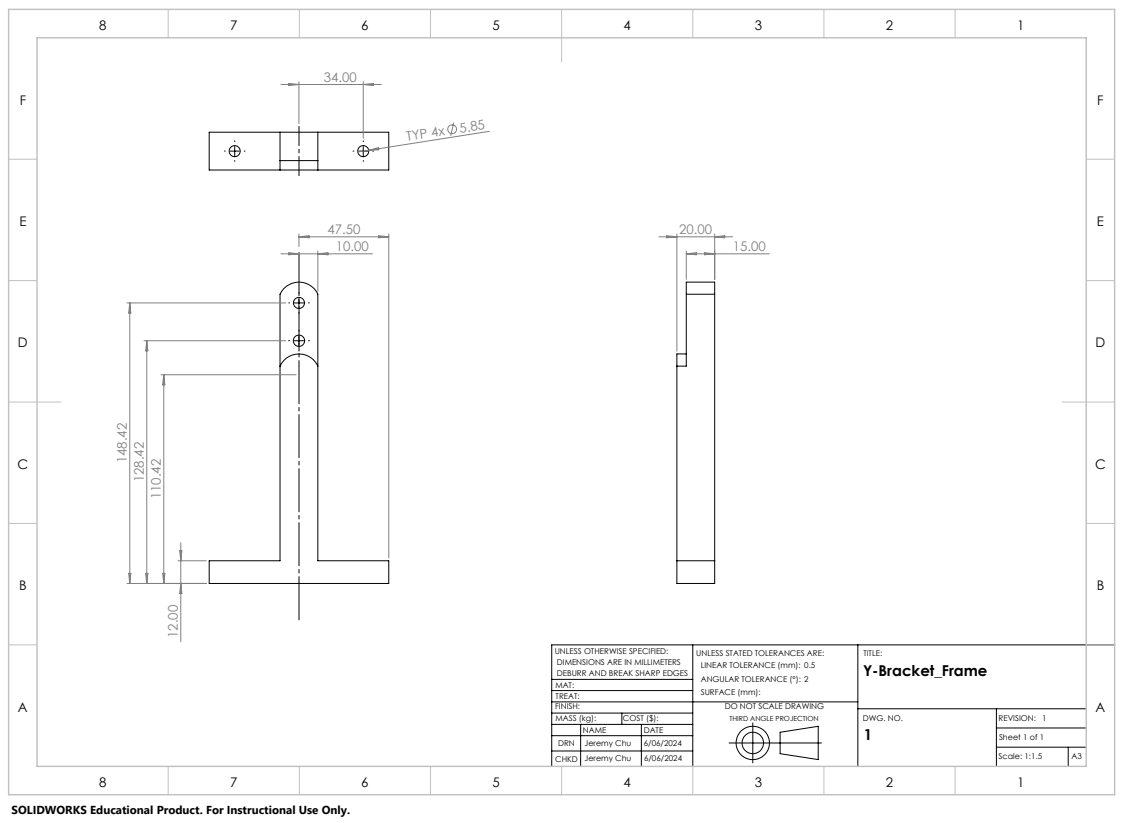
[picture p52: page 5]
TYP 4x 5.85; Y-Bracket_Frame; TITLE:; DWG. NO.; REVISION:; Sheet 1 of 1; Scale: 1:1.5

UNLESS OTHERWISE SPECIFIED:
DIMENSIONS ARE IN MILLIMETERS
DEBURR AND BREAK SHARP EDGES
MAT:
TREAT:

UNLESS STATED TOLERANCES ARE:
LINEAR TOLERANCE (mm):
ANGULAR TOLERANCE (°):
SURFACE (mm):

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

7.00

17.00

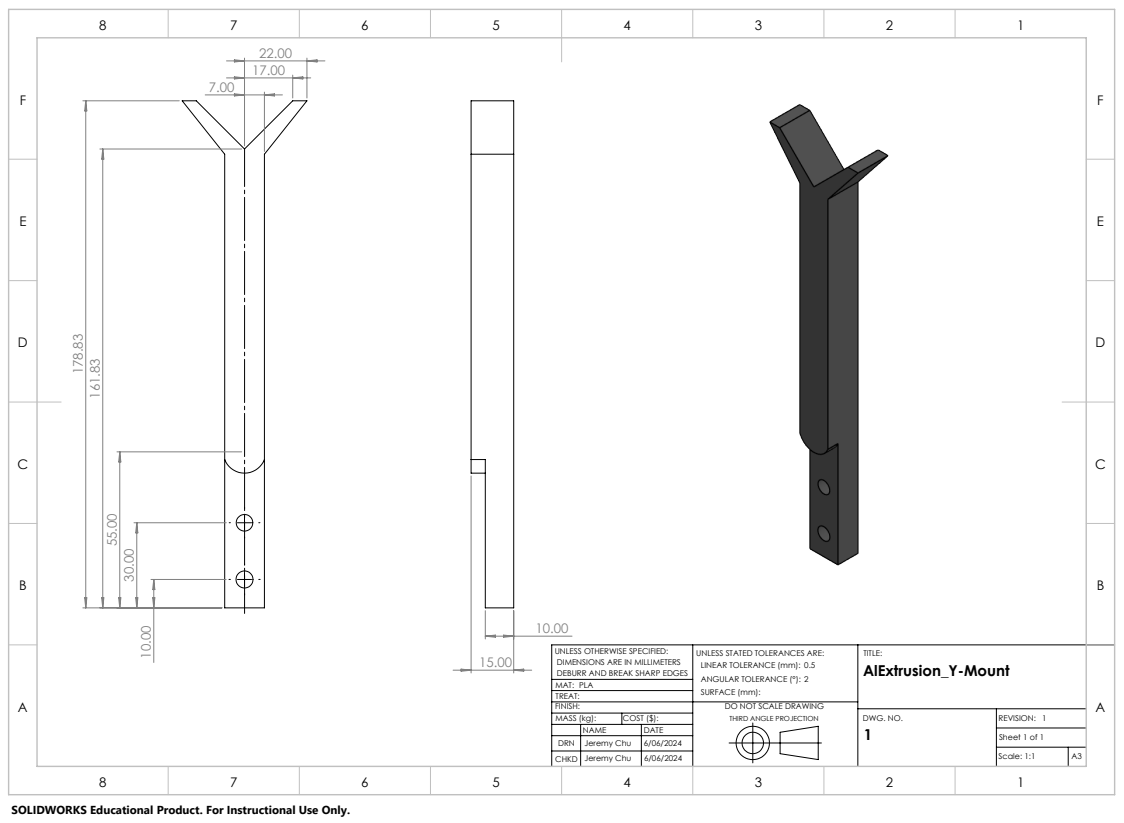
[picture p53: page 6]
AlExtrusion_Y-Mount; TITLE:; DWG. NO.; REVISION:; Sheet 1 of 1; Scale: 1:1

UNLESS OTHERWISE SPECIFIED:
DIMENSIONS ARE IN MILLIMETERS
DEBURR AND BREAK SHARP EDGES
MAT:
PLA
TREAT:

UNLESS STATED TOLERANCES ARE:
LINEAR TOLERANCE (mm):
ANGULAR TOLERANCE (°):
SURFACE (mm):

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

F | F

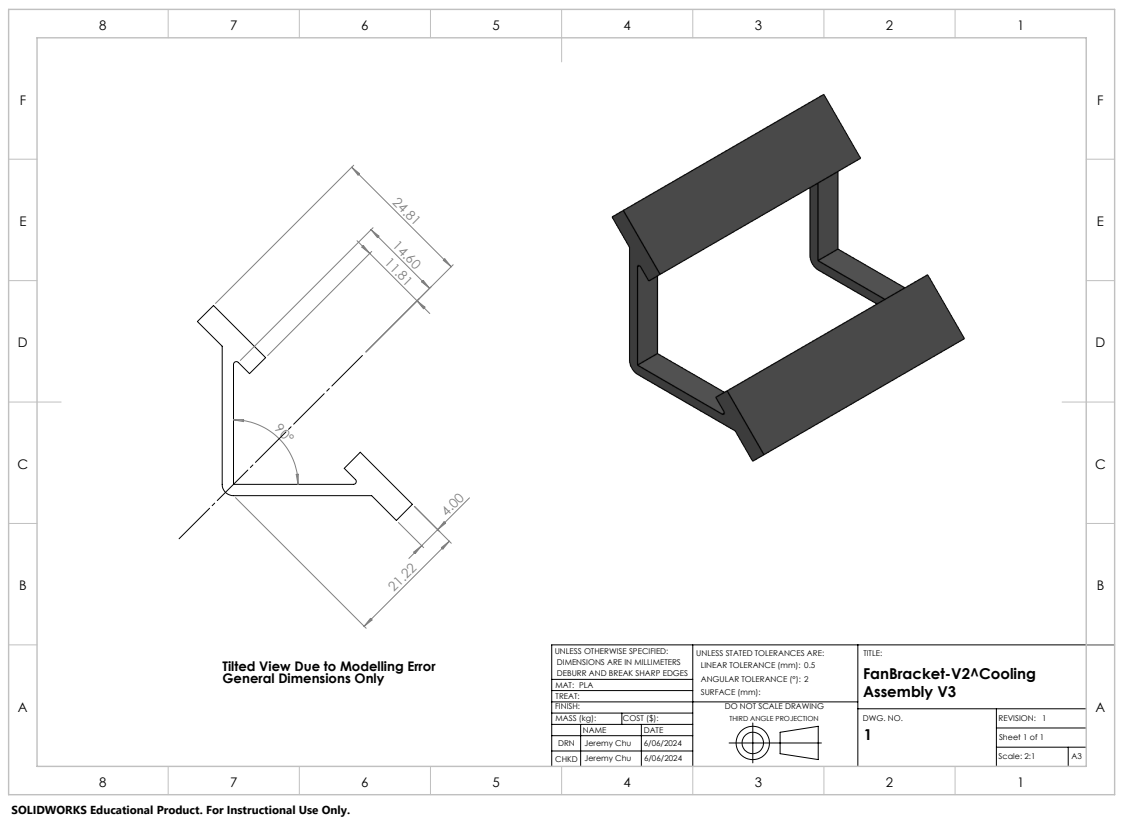
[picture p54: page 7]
MAT: TREAT:; DWG. NO.; REVISION:; Sheet 1 of 1; Scale: 2:1; PLA

UNLESS OTHERWISE SPECIFIED: DIMENSIONS ARE IN MILLIMETERS DEBURR AND BREAK SHARP EDGES | UNLESS STATED TOLERANCES ARE: LINEAR TOLERANCE (mm): 0.5 2 ANGULAR TOLERANCE (°): SURFACE (mm): | TITLE: FanBracket-V2^Cooling Assembly V3

Tilted View Due to Modelling Error
General Dimensions Only

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

F | F

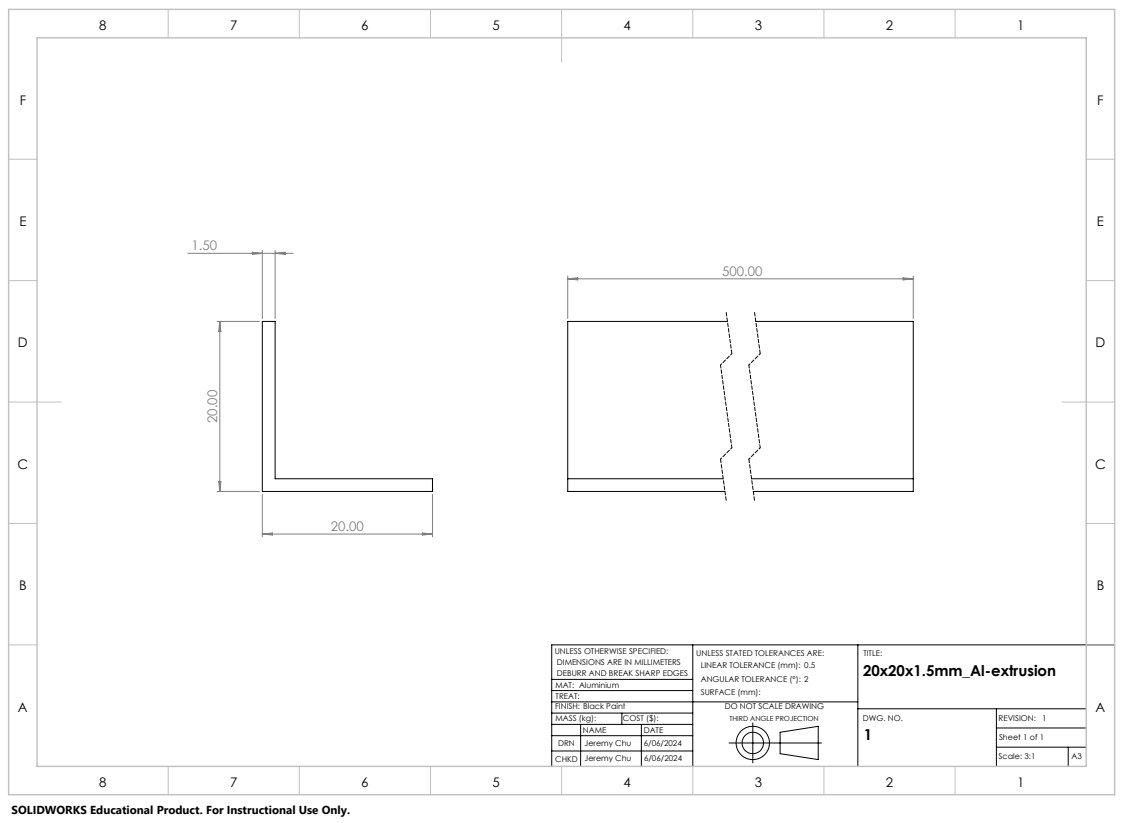
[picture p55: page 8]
MAT: TREAT:; DWG. NO.; REVISION:; Sheet 1 of 1; Scale: 3:1; Aluminium

UNLESS OTHERWISE SPECIFIED: DIMENSIONS ARE IN MILLIMETERS DEBURR AND BREAK SHARP EDGES | UNLESS STATED TOLERANCES ARE: LINEAR TOLERANCE (mm): 2 0.5 ANGULAR TOLERANCE (°): SURFACE (mm): | TITLE: 20x20x1.5mm_Al-extrusion

FINISH: Black Paint | DO NOT SCALE DRAWING THIRD ANGLE PROJECTION
MASS (kg): | COST ($):
NAME | DATE
DRN | Jeremy Chu | 6/06/2024

325.00
17.50

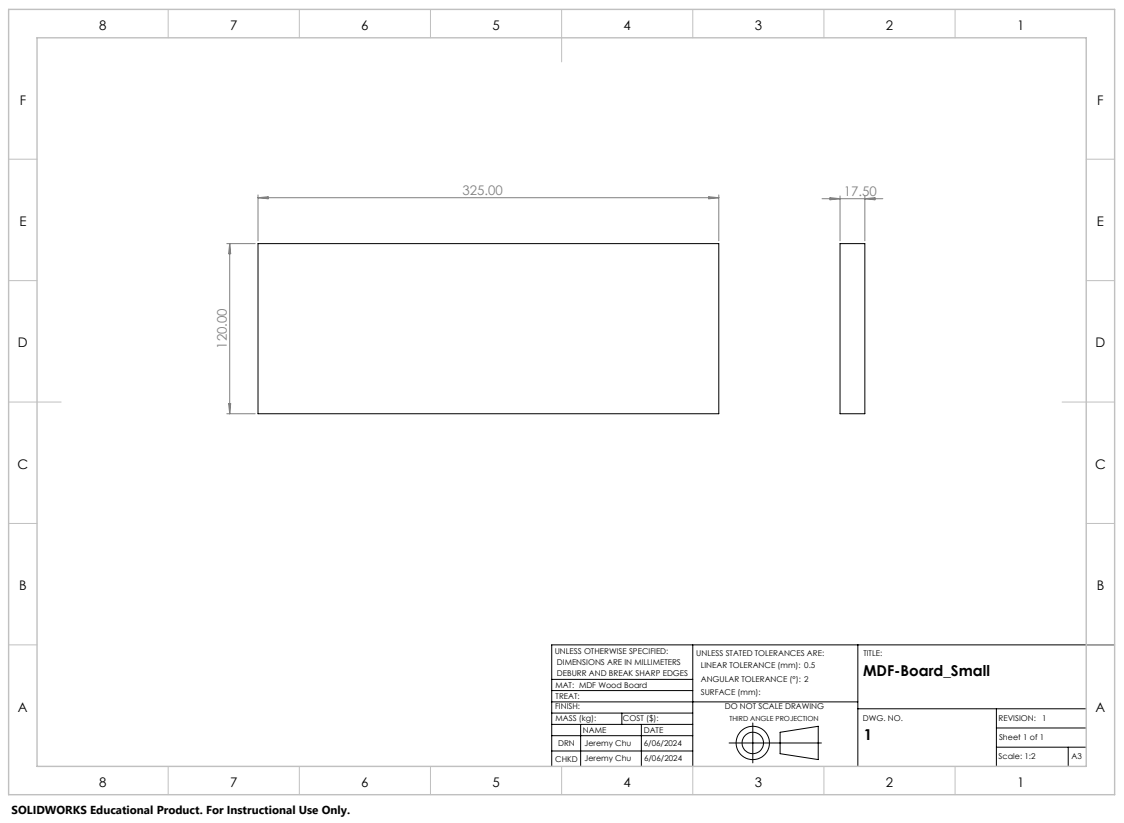
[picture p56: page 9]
DWG. NO.; REVISION:; Sheet 1 of 1; Scale: 1:2

UNLESS OTHERWISE SPECIFIED: DIMENSIONS ARE IN MILLIMETERS DEBURR AND BREAK SHARP EDGES | UNLESS STATED TOLERANCES ARE: LINEAR TOLERANCE (mm): 2 0.5 ANGULAR TOLERANCE (°): SURFACE (mm): | TITLE: MDF-Board_Small

MAT:
MDF Wood Board
TREAT:

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

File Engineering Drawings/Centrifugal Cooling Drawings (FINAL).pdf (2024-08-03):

# Engineering Drawings for:

# Centrifugal Cooling

# Filament Spooling Team

## University of Technology Sydney

## for 43019 Design in Mechanical and Mechatronic Systems - Autumn 2024

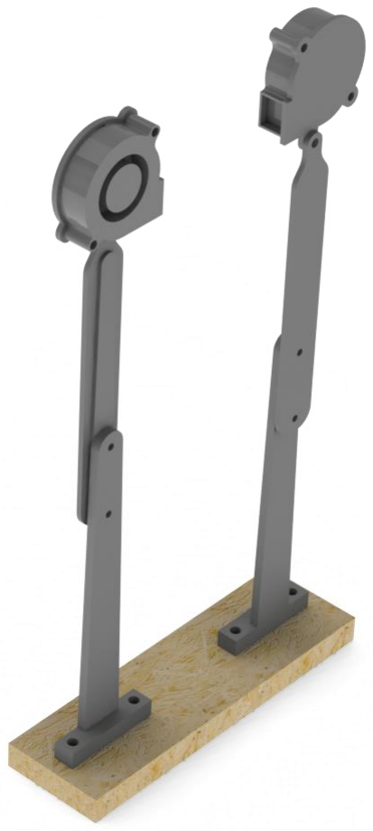
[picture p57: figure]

# Design and Drawings: Jeremy Chu

CentrifugalCooling Assembly | 2
CentrifugalFan-Base | 3
CentrifugalFan-HeightArm | 4
CentrifugalFan-Bracket | 5
CentrifugalCooling-WoodBase | 6

## Adjustable angle by Wing nut (not shown)

2

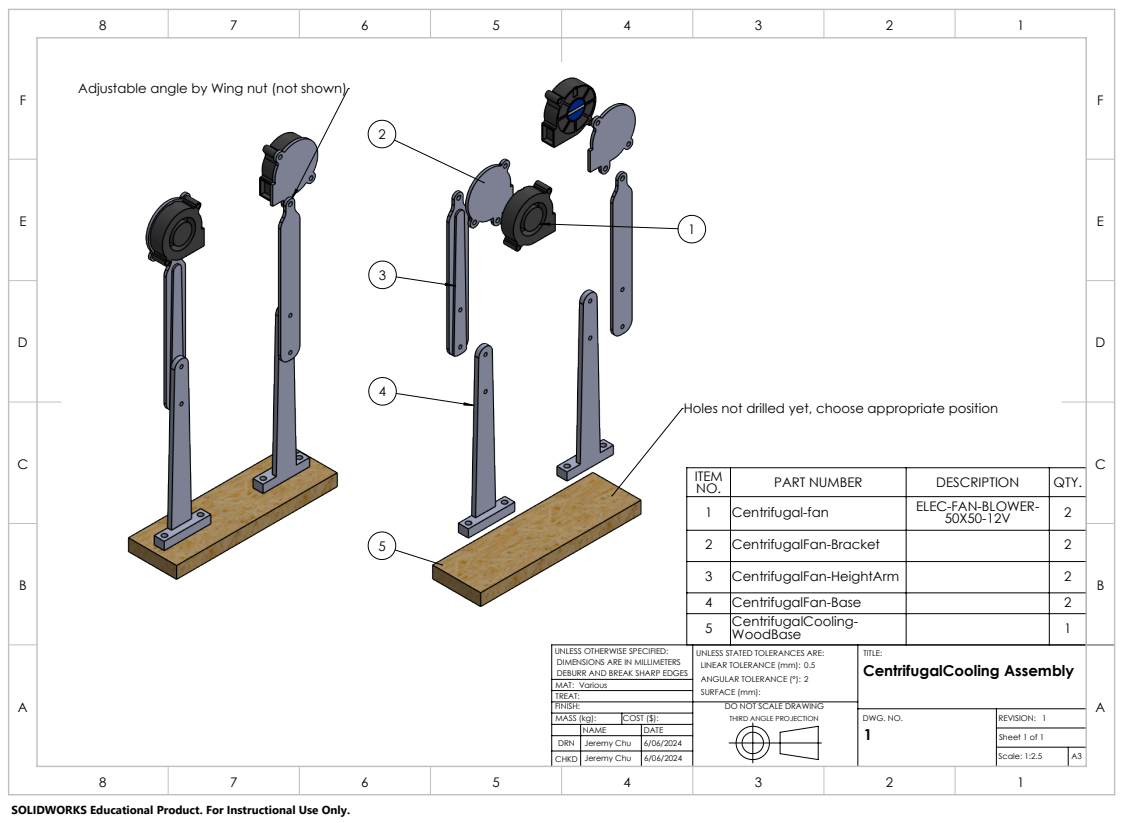
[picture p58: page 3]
MAT: TREAT:; DWG. NO.; REVISION:; Sheet 1 of 1; Various

Holes not drilled yet, choose appropriate position

ITEM NO. | PART NUMBER | DESCRIPTION | QTY.
1 | Centrifugal-fan | ELEC-FAN-BLOWER-50X50-12V | 2

2 | CentrifugalFan-Bracket | | 2
3 | CentrifugalFan-HeightArm | | 2
4 | CentrifugalFan-Base | | 2
5 | CentrifugalCooling-WoodBase | | 1

UNLESS OTHERWISE SPECIFIED: DIMENSIONS ARE IN MILLIMETERS DEBURR AND BREAK SHARP EDGES | UNLESS STATED TOLERANCES ARE: LINEAR TOLERANCE (mm): 2 0.5 ANGULAR TOLERANCE (°): SURFACE (mm): | TITLE: CentrifugalCooling Assembly

FINISH: | DO NOT SCALE DRAWING THIRD ANGLE PROJECTION
MASS (kg): | COST ($):
NAME | DATE
DRN | Jeremy Chu | 6/06/2024
CHKD | Jeremy Chu

Scale: 1:2.5 | A3

SOLIDWORKS Educational Product. For Instructional Use Only.

5.00

25.00

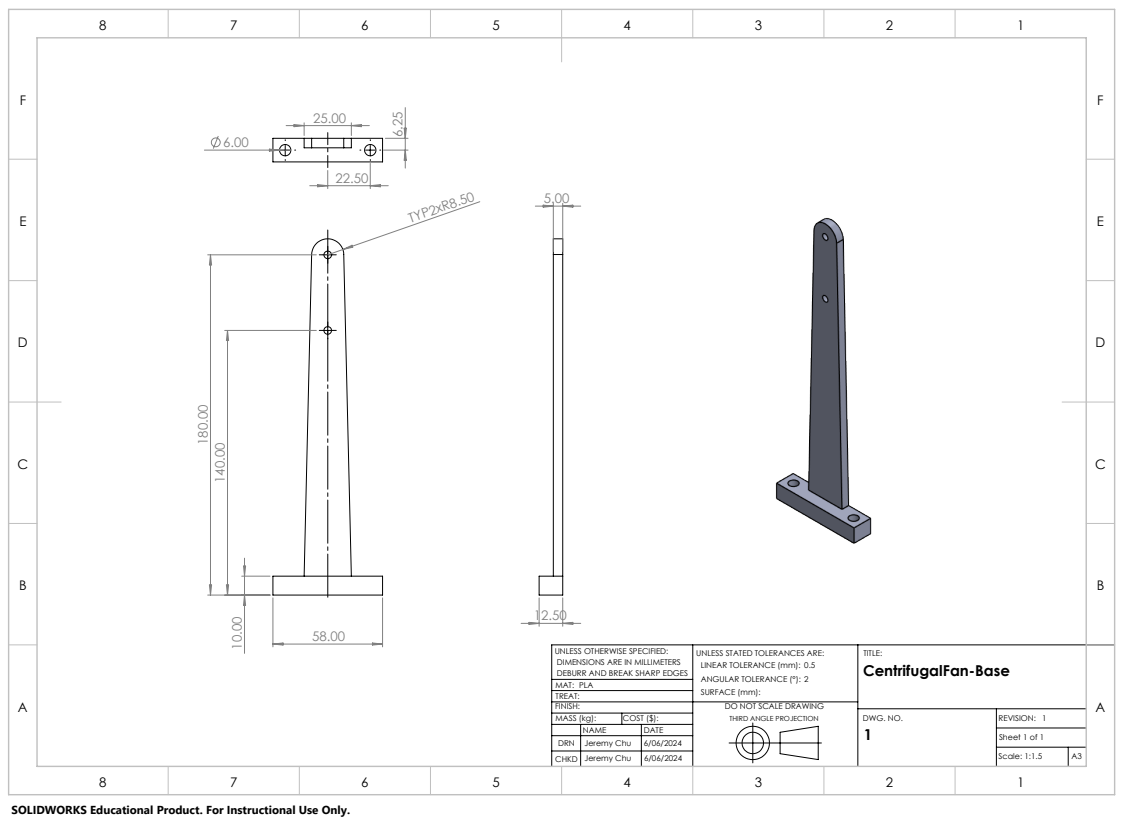
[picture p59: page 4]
TYP2xR8.50; CentrifugalFan-Base; TITLE:; DWG. NO.; REVISION:; Sheet 1 of 1; Scale: 1:1.5

UNLESS OTHERWISE SPECIFIED:
DIMENSIONS ARE IN MILLIMETERS
DEBURR AND BREAK SHARP EDGES
MAT:
PLA
TREAT:

UNLESS STATED TOLERANCES ARE:
LINEAR TOLERANCE (mm):
ANGULAR TOLERANCE (°):
SURFACE (mm):

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

F | F

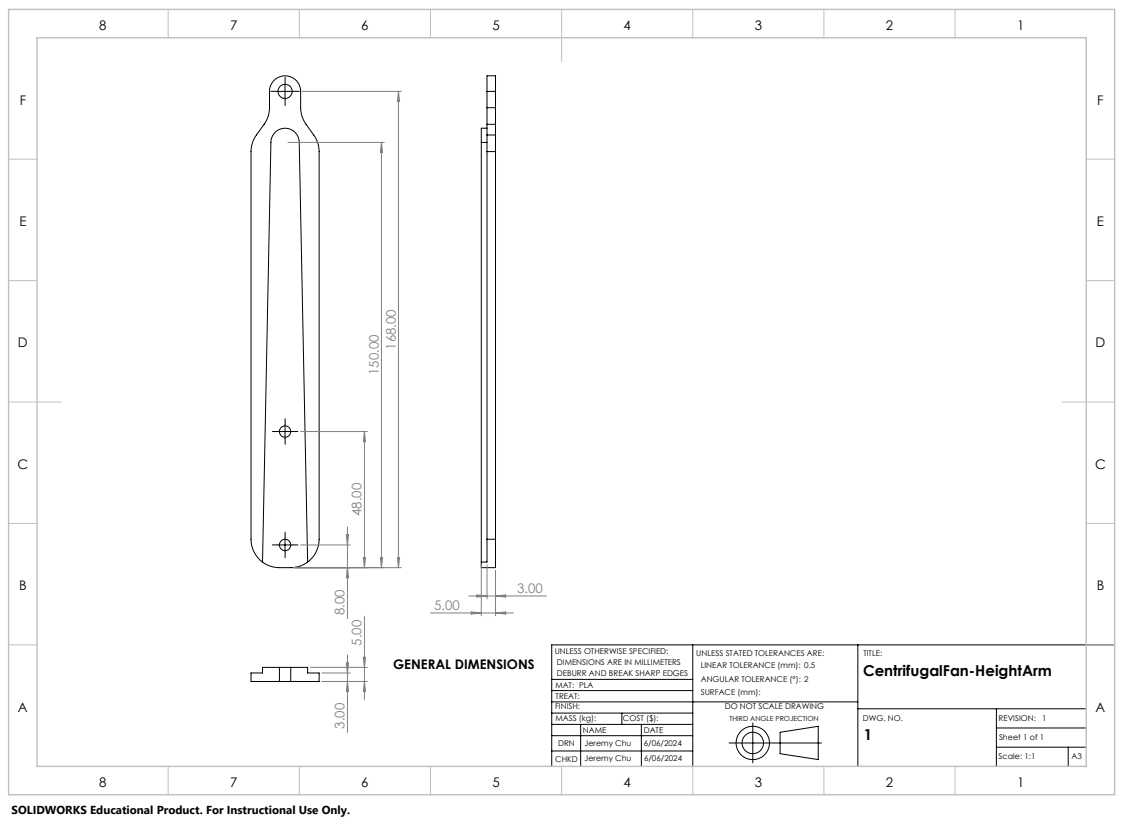
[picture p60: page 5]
GENERAL DIMENSIONS; MAT: TREAT:; DWG. NO.; REVISION:; Sheet 1 of 1; Scale: 1:1; PLA

UNLESS OTHERWISE SPECIFIED: DIMENSIONS ARE IN MILLIMETERS DEBURR AND BREAK SHARP EDGES | UNLESS STATED TOLERANCES ARE: LINEAR TOLERANCE (mm): 2 0.5 ANGULAR TOLERANCE (°): SURFACE (mm): | TITLE: CentrifugalFan-HeightArm

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

19.00

47.85

TYP 3X 4.60; SIMPLIFIED DRAWING; MAT: TREAT:; DWG. NO.; REVISION:; Sheet 1 of 1; Scale: 2:1; PLA

UNLESS OTHERWISE SPECIFIED: DIMENSIONS ARE IN MILLIMETERS DEBURR AND BREAK SHARP EDGES | UNLESS STATED TOLERANCES ARE: LINEAR TOLERANCE (mm): 2 0.5 ANGULAR TOLERANCE (°): SURFACE (mm): | TITLE: CentrifugalFan-Bracket

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

F | F

DWG. NO.; REVISION:; Sheet 1 of 1; Scale: 1:1

UNLESS OTHERWISE SPECIFIED: DIMENSIONS ARE IN MILLIMETERS DEBURR AND BREAK SHARP EDGES | UNLESS STATED TOLERANCES ARE: LINEAR TOLERANCE (mm): 0.5 2 ANGULAR TOLERANCE (°): SURFACE (mm): | TITLE: CentrifugalCooling-WoodBase

MAT:
MDF Wood Board
TREAT:

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

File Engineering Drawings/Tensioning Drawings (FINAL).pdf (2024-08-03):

# Engineering Drawings for:

# Tensioning (Puller) Version 3

# Filament Spooling Team

## University of Technology Sydney

## for 43019 Design in Mechanical and Mechatronic Systems - Autumn 2024


# Design and Drawings: Jeremy Chu

P-V3 Stationary Bearing Assembly(A) | 2
P-V3 Bearing Housing(SA) | 4
P-V3 Roller Assembly(SA) | 5
P-V3 BasePlate | 7
P-V3 Stationary Bearing Body | 8
Nema17-StepperMotor Bracket | 9
StepperMotor-MMC(6627T64) | 10
P-V3 TopCap | 11
P-V3 TPU Roller | 12
P-V3 Roller Shaft | 13
P-V3 Roller Small Shaft | 15
P-V3 Metal Shaft for Rollers | 16
BallBearing_V1 | 17
CompSpring_V2 | 18
GT2-20T-Pulley | 19
GT2-60T-Pulley | 20

F | F

MAT: TREAT:; DWG. NO.; REVISION:; Sheet 1 of 2; Various

THIRD ANGLE PROJECTION ¹⁵⁴.98

UNLESS OTHERWISE SPECIFIED: DIMENSIONS ARE IN MILLIMETERS DEBURR AND BREAK SHARP EDGES | UNLESS STATED TOLERANCES ARE: LINEAR TOLERANCE (mm): 0.5 2 ANGULAR TOLERANCE (°): SURFACE (mm): | TITLE: P-V3 Stationary Bearing Assembly

FINISH: | DO NOT SCALE DRAWING
MASS (kg): | COST ($):
NAME | DATE
DRN | Jeremy Chu | 25/05/2024
CHKD | Jeremy Chu

Scale: 1:2 | A3

SOLIDWORKS Educational Product. For Instructional Use Only.

14

F | F

Nema-17 Stepper; Motor; P-V3 Stationary Bearing; Assembly; TITLE:; DWG. NO.; REVISION:; Sheet 2 of 2; Scale: 1:1.8

ITEM NO. | PART NUMBER | DESCRIPTION | QTY.
1 | BallBearing_V1 | 688ZZ | 4
2 | P-V3 Bearing Housing | | 2
3 | CompSpring_V2 | Unknown k | 4
4 | P-V3 Stationary Bearing Body | | 2
5 | P-V3 Roller Shaft | | 2
6 | P-V3 Roller Small Shaft | | 2
7 | P-V3 TPU Roller | | 2
8 | GT2-60T-Pulley | W=6mm | 1
9 | P-V3 Metal Shaft for Rollers | | 1
10 | Nema17-StepperMotor Bracket | | 1

12 | GT2-20T-Pulley | W=6mm | 1
13 | P-V3 BasePlate | | 1
14 | P-V3 TopCap | | 1
15 | GT2 200mm TimingBelt | GT2 W=6mm, 200mm | 1

UNLESS OTHERWISE SPECIFIED:
DIMENSIONS ARE IN MILLIMETERS
DEBURR AND BREAK SHARP EDGES
MAT:
TREAT:

UNLESS STATED TOLERANCES ARE:
LINEAR TOLERANCE (mm):
ANGULAR TOLERANCE (°):
SURFACE (mm):

FINISH: | DO NOT SCALE DRAWING THIRD ANGLE PROJECTION
MASS (kg): | COST ($):
NAME | DATE
DRN | Jeremy Chu | 25/05/2024

F | F

MAT: TREAT:; DWG. NO.; REVISION:; Sheet 1 of 1; Scale: 3:1; Various

UNLESS OTHERWISE SPECIFIED: DIMENSIONS ARE IN MILLIMETERS DEBURR AND BREAK SHARP EDGES | UNLESS STATED TOLERANCES ARE: LINEAR TOLERANCE (mm): 2 0.5 ANGULAR TOLERANCE (°): SURFACE (mm): | TITLE: P-V3 Bearing Housing(SA)

FINISH: | DO NOT SCALE DRAWING THIRD ANGLE PROJECTION
MASS (kg): | COST ($):
NAME | DATE
DRN | Jeremy Chu | 26/05/2024

F | F

Driven Subassembly; MAT: TREAT:; DWG. NO.; REVISION:; Sheet 1 of 2; Scale: 1:1

UNLESS OTHERWISE SPECIFIED: DIMENSIONS ARE IN MILLIMETERS DEBURR AND BREAK SHARP EDGES | UNLESS STATED TOLERANCES ARE: LINEAR TOLERANCE (mm): 2 0.5 ANGULAR TOLERANCE (°): SURFACE (mm): | TITLE: P-V3 Roller Assembly(SA)

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

F | F

Driver Assembly; MAT: TREAT:; DWG. NO.; REVISION:; Sheet 2 of 2; Scale: 1:1

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

4x5.43 | 4x7.87

51.00

MAT: TREAT:; DWG. NO.; REVISION:; Sheet 1 of 1; Scale: 1:1.2; PLA

UNLESS OTHERWISE SPECIFIED: DIMENSIONS ARE IN MILLIMETERS DEBURR AND BREAK SHARP EDGES | UNLESS STATED TOLERANCES ARE: LINEAR TOLERANCE (mm): 2 0.5 ANGULAR TOLERANCE (°): SURFACE (mm): | TITLE: P-V3 BasePlate

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

17.00
F | F

P-V3 Stationary Bearing Body; TITLE:; DWG. NO.; REVISION:; Sheet 1 of 1; Scale: 1:1.3

UNLESS OTHERWISE SPECIFIED:
DIMENSIONS ARE IN MILLIMETERS
DEBURR AND BREAK SHARP EDGES
MAT:
PLA
TREAT:

UNLESS STATED TOLERANCES ARE:
LINEAR TOLERANCE (mm):
ANGULAR TOLERANCE (°):
SURFACE (mm):

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

3.25

F | F

MAT: TREAT:; DWG. NO.; REVISION:; Sheet 1 of 1; Scale: 1.4:1; PLA
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
